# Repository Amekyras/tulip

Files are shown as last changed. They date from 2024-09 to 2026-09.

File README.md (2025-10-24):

# Welcome to TULIP 2.0

>"Everything will be alright as long as you have your -ing potato." - Mr. Tulip, to Mr. Pin, _The Truth_, by Terry Pratchett

>"See a pin and pick it up, and all day long you’ll have a pin!" - Stanley Howler, _Going Postal_, by Terry Pratchett

## A full pin mod for the AB motor mounts, XY gantry joints and front idler tensioners for the Voron v0.2
 - AB motors are mounted solidly to the frame, meaning no more shunting them back and forth with a bulky tensioning nut
 - AB motor shafts are held in double shear with an extra bearing, lowering radial force on the motor bearings
 - Tension is now applied through an M3 screw in the front idlers, and ALL bearing stacks run on pins rather than screws
 - Both MGN7H (stock) and MGN9C X rails are supported, WITH NO TRAVEL LOSS
 - Standard 3mm off-the-shelf pins, for those unable to cut their own
 - LazyCam support
 - Fysetc X light gantry compatibility (use standard XY joints)
 - Mamabot.io X light gantry support
 - Nema 17 AB Motor Mount Beta 
 - Nema 14 - 35mm Shaft Motor Mount Beta
 - Live Idler XY joints + Tension Idlers

## Installation
Go to the [Releases Page](https://github.com/Amekyras/tulip/releases) and download the .zip file from the latest release.

## Renders

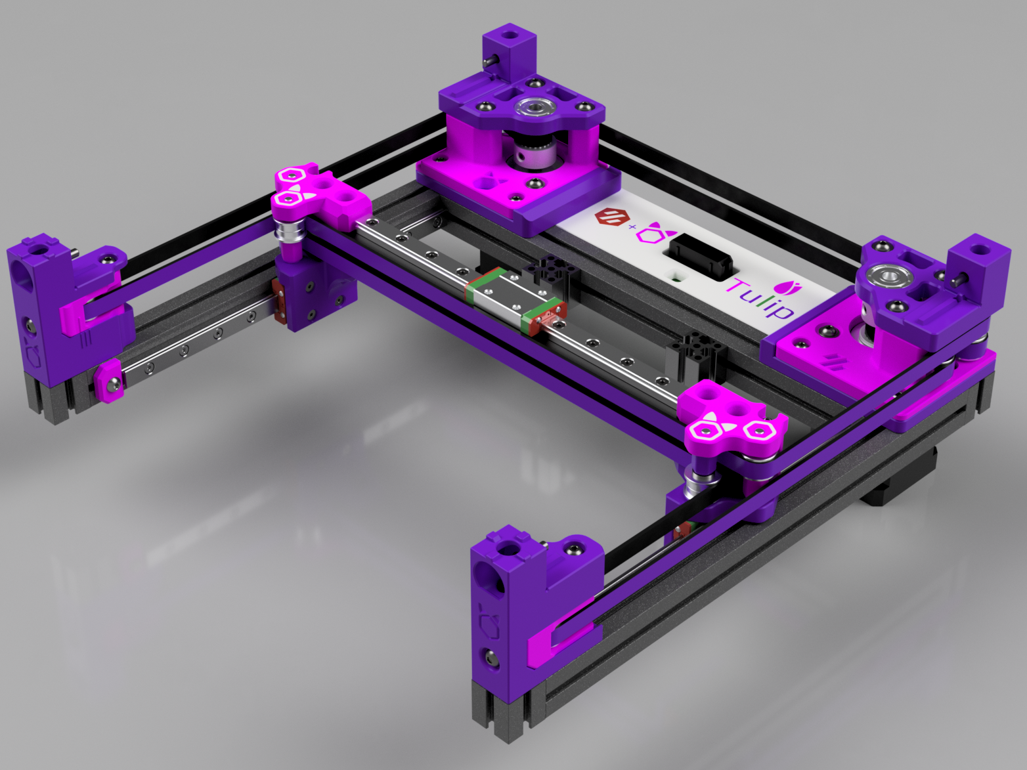
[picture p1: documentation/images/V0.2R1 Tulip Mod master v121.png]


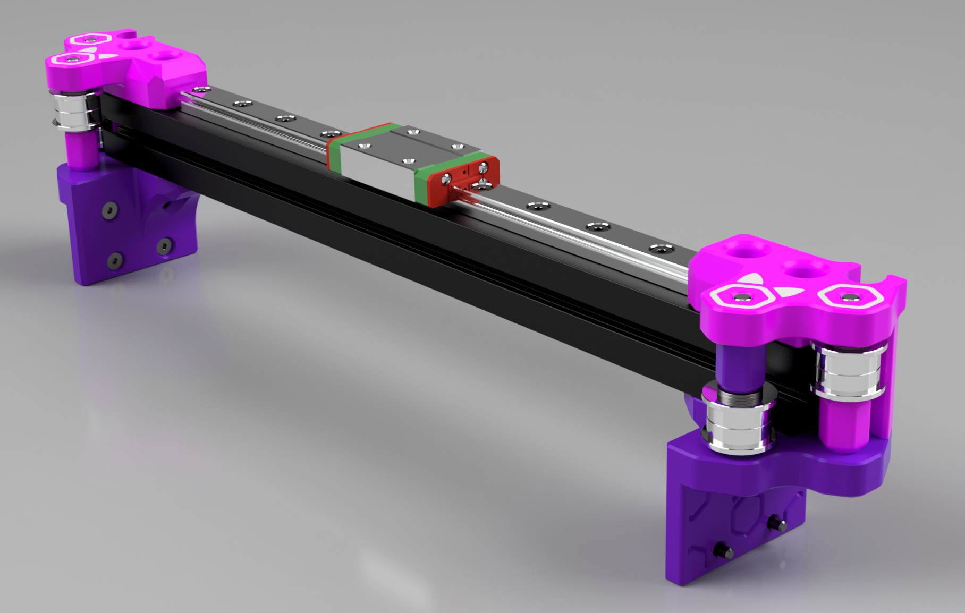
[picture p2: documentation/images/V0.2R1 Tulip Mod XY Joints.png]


| Idlers | XY Joints |
| :---: | :---: |
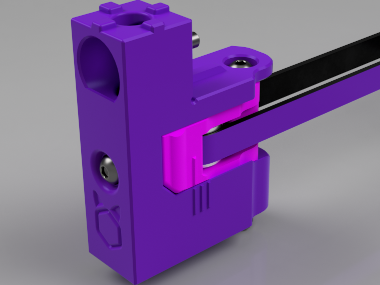
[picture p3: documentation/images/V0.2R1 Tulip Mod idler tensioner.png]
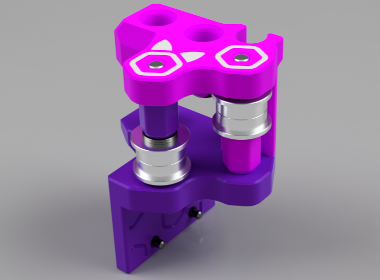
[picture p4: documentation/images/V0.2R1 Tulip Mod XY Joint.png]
|  |  |
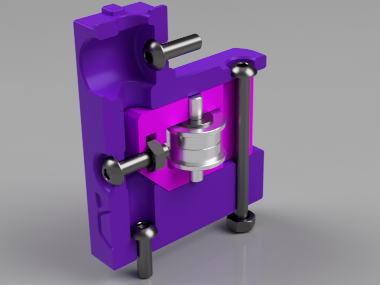
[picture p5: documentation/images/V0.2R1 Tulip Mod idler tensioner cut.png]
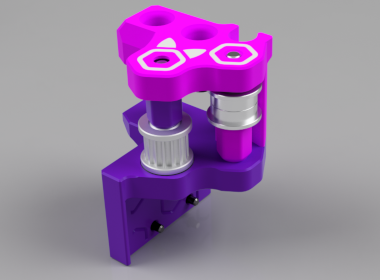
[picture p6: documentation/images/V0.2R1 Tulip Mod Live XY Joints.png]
|  |  |

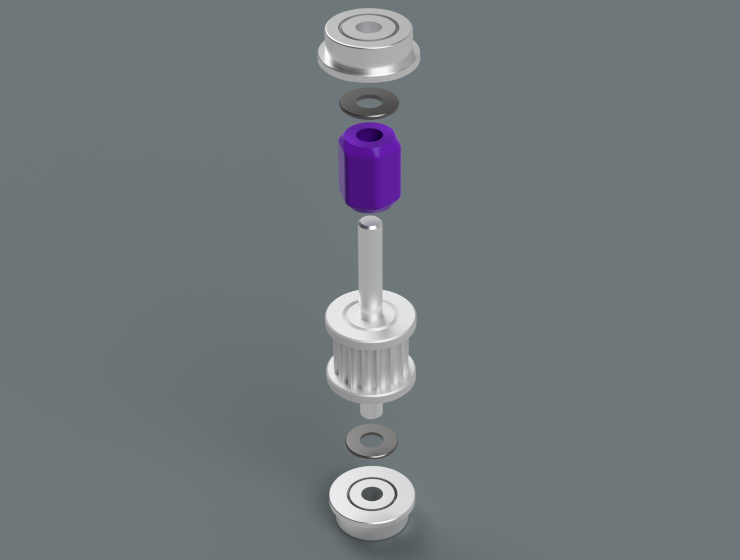
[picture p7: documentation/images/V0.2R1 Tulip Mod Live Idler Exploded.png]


----

> **Note - for LazyCam idlers you will require some extra printed parts to complete found [here](https://www.printables.com/model/533483-voron-02-lazycams-tool-free-locking-idlers-models)**

Parts required are; 

- LazyCams_C-A CamArm_v1.stl
- LazyCams_C-A CamLock_v1.stl

- LazyCams_C-B CamArm_v1.stl
- LazyCams_C-B CamLock_v1.stl

---

## Bill of Materials (BOM)

### Idler / Tensioner BOM

| **Part** | **Quantity** | **Notes / Links** | 
| :--- | :--- | :--- |
| Pin M3x18mm | 2 | [KB-3D](https://kb-3d.com/store/hardware/143-3mm-bearing-steel-shafts-various-lengths-1642291225169.html) / [AliExpress](https://www.aliexpress.us/item/3256804639701799.html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) | 
| M2x10 Self Tapper | 4 |  | 
| M3 Hexnut | 4 |  | 
| M3x0.5mm Washer / Shim | 4 |  | 
| M3x10 BHCS | 4 |  | 
| M3x12 BHCS | 2 |  | 
| M3x35 BHCS | 2 |  | 
| F623 Bearing | 4 |  | 

---

### AB Motor Mount BOM

| **Part** | **Quantity** | **Notes / Links** | 
| :--- | :--- | :--- |
| 625-ZZ/2RS Bearing | 2 |  | 
| GT2 20T 6mm Pulley | 2 |  | 
| M3 Hexnut | 6 |  | 
| M3 Threaded Insert | 4 |  | 
| M3x0.5mm Washer / Shim | 20 |  | 
| M3x8 BHCS | 2 |  | 
| M3x10 BHCS | 4 |  | 
| M3x12 BHCS | 4 |  | 
| M3x30 BHCS | 6 |  | 
| Pins M3x30mm | 4 | [KB-3D](https://kb-3d.com/store/hardware/143-3mm-bearing-steel-shafts-various-lengths-1642291225169.html) / [AliExpress](https://www.aliexpress.us/item/3256804639701799.html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) | 
| F623 Bearing | 12 |  | 

---

### XY Joint BOM

| **Part** | **Quantity** | **Notes / Links** | 
| :--- | :--- | :--- |
| M3x6 BHCS | 2 |  | 
| M2x6 FHCS | 8 |  | 
| M3x8 BHCS | 4 |  | 
| Pins M3x30mm | 4 | [KB-3D](https://kb-3d.com/store/hardware/143-3mm-bearing-steel-shafts-various-lengths-1642291225169.html) / [AliExpress](https://www.aliexpress.us/item/3256804639701799.html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) | 
| M3x0.5mm Washer / Shim | 16 |  | 
| F623 Bearing | 8 |  | 

---

### Live Idler XY Joint BOM

| **Part** | **Quantity** | **Notes / Links** | 
| :--- | :--- | :--- |
| M3x6 BHCS | 2 |  | 
| M2x6 FHCS | 8 |  | 
| M3x8 BHCS | 4 |  | 
| XY Pins M3x30 | 4 | [KB-3D](https://kb-3d.com/store/hardware/143-3mm-bearing-steel-shafts-various-lengths-1642291225169.html), [AliExpress](https://www.aliexpress.us/item/3256804639701799.html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) | 
| M3x0.5 Washer / Shim | 12 |  | 
| F623 Bearing | 8 |  | 
| 16T Solid Idler | 2 | [Alchemy3d](https://alchemy3d.de/products/active-idlers-5mm-id-16t-for-6mm-belt), [Filastruder](https://www.filastruder.com/collections/gates/products/gates-2gt-pulley-custom-no-grub-set-screw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), [3dkatten](http://3dkatten.eu/products/custom-16t-2gt-3mm-id-live-shaft-idler) | 

----

NEW Pin Hole Sizing for Tulip should mean NO MORE REAMING! but if you still have trouble fitting your pins then refer to this guide

> **Note - For PIN FITTING GUIDE you can find it [here](https://github.com/Amekyras/tulip/tree/main/PIN%20GUIDE)**

----

**Links to original source material**

https://github.com/VoronDesign/Voron-0

https://vorondesign.com

https://github.com/akinferno/Voron0/tree/main/LazyCams

https://github.com/ruiqimao/VoronUsers/tree/v0.2-mgn9c/printer_mods/ruiqimao/V0.2_MGN9C_X

**GNU Terry Pratchett**

----

**special thanx for all thoes who have helped with feedback and improvement ideas to get Tulip as good as it is!**

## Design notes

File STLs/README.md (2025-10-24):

# PRINTING GUIDE

All parts print with standard VORON Settings!

----

## CHOOSE YOUR JOURNEY

----

### OEM Tulip - The Path of Least Resistance

- One set of
  - AB Mounts
  - XY Joints
  - Idler Tensioners
  - Umbilical Covers
  - Tools & Jigs

----  

### LIVE Tulip - The Intrepid Adventurer

- One set of
  - AB Mounts
  - Live XY Joints
  - Live Idler Tensioners
  - Umbilical covers
  - Tools & Jigs

----

### EXPERIMENTAL Tulip - The Undaunted Explorer

- A Choice of optional parts are available to you to experiment with
- WARNING !!! This section is for those who have good knowledge of their printer, understand the CAD and work / assembly of these parts

  - S35 AB Mounts - For 35mm Shaft Nema14 Motors
  - Nema17 AB Mounts
  - Nema17 AWD AB Mounts
  - Mamababot.IO XY joints

----

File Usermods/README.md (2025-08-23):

| Creator | Mod title | Description |
| --- | --- | --- |
| hawk16zz | [2mm taller parts](<./hawk16zz/2mm%20Taller%20ABs%20and%20Blocks>)| 2mm taller mod to address heights descripencies due to door mods and/or panels|

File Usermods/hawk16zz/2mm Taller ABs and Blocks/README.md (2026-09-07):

2026-09-06: Updated for Tulip v2.1

This mod adds 2mm to the height of A/B tops and the tensioner block parts to address issues with the LDO fridge door kit sitting proud on some builds or if you need them for full height panels.

The increase in height also means you don't need the lazycam specific tensioner carriage as they are no long are in the path of the cam lever arm.

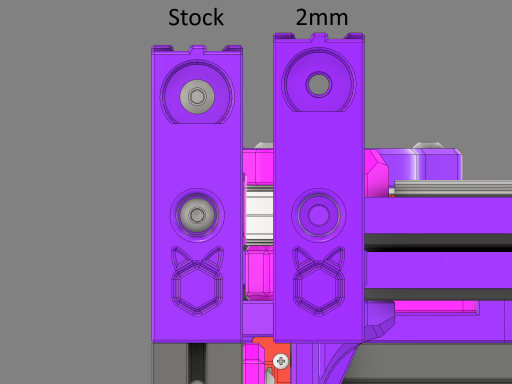
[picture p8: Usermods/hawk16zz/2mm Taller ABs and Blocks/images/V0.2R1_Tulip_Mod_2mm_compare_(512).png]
A comparison of stock v 2mm taller.


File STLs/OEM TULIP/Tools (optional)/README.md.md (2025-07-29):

The TOOLS provided for Tulip Mod carry a certain element of risk to the user!

if not used correctly these can injure / maim you so please use them wisely!

They are intended to help you cut and / or install parts for Tulip Mod.

If you have any doubt or questions about the safe use of these tools please reach out on the Voron Discord to either @driftrotor or @amekyras and we will do our best to guide you and answer any questions you might have.
We accept no resposibility for any injury / damage to property or persons involved and all use of these tools is solely the resposibility of the person using them.

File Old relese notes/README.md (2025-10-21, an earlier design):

----

### 01/12/24

CAD V33 release

updated the pin cutting tool to give 18mm pins (as this is now the standard)

STL's have been updated

28/11/24

CAD v32 release

small amendments to supporting drawing

removal of 16mm pin tension idlers - in favour of better 18mm pin version (also to simplify and cause less confusion)

NEW addition of Nema 14 - 35mm shaft CAD and STL's

NEW addition of LIVE IDLER CAD for XY joints to have solid toothed idler and live pins
STL's have been added

----

### 10/11/24

CAD v31 release

Added umbilical Cover Plates (with + without Bowden Hole) and MMU versions

Added Picobilical Strain Relief Beta (MMU)

----

### 04/11/24

CAD v29 release

House keeping in CAD - Created componants for all bodies, Some name corrections, Reduced Materials

18mm Pin version of the front Idler Tensioners have been added for those who are struggling to find 16mm Pins, These also have LazyCam support
these are also recomended to those wishing to use GT3 belts

X Light Gantry (MamaBot.io) Beta is now included
> **Note - This is NOT compatible with the Fysetc X Light Gantry, instead use standard XY Joints**

Nema 17 AB Motor Mount Beta added for testing

ReadMe's added for some folders - please make sure you read them

STL's added

BOM amended + PDF format added

ALL STL's updated to latest CAD version

ALL Pin Holes have a new size (this should work for a better fit withoit the reeming)

----

### 16/09/24

CAD v28 release

Both Standard and LazyCAM static bodies have has the access hole size changed (for the front fixing into the extrusion) so that longer screws can be used and dropped in from the top.

A NEW motor "Pully Tool" has been made to measure from the motor tops rather than from the top of the shaft

BOM has been updated to show "Washers / Shims" for the bearing stacks

XY_Upper_Joint Fixings changed from M3x6mm to M3x8mm on CAD

PIN GUIDE has been added to help users get the best from TULIP

MGN9H BETA (yes H) has been added for those wanting to use this type of rail setup. All printed parts needed are in the STL's frolder MGN9H.
> **Note - A 160mm Rail is required for full travel**

----

### 04/09/24

CAD v27 release

Amended Pin hole depth on parts

- Top_Mount_A_MGN9C_x1
- Top_Mount_B_MGN9C_x1

Motor "Pully Tool" has now been added to help get them in the right place

Picture of the tool has been added to the PICS folder

STL's have been updated for the latest change for the parts affected

----

### 24/08/24

CAD v26 release

CAD names have been updated to be consistant with the STL names and the [a] for accent colour marking has also been added. Corrected a mistake where the Voron Logo was mirrored on Mid_Mount_A_x1.

STL's Updated to latest Names denoting the [a] for accent colours. corrected Mid_Mount_A_x1 STL

----

### 08/08/24

CAD v25 release

Idler tensioners static body had printability update to make B side easier to print (less chance to warp off the bed)

tensioner upers had changes to work with new static bodies

Tensioner lowers captive nut minor geometry changes - better pre-engagement with tension screw - reduced hole size after captive nut to act as tension screw "nylock"

LazyCam static bodies added for those wishing to use the LazyCam system (type C)

----

### 10/07/24

CAD v24 release

Idler tensioners static body is now one piece and printed on its side

Idler tensioners lock screw is now static with slot in tensioner parts

XY joints had some holes resized and some minor corrections

Spacers - new fillet chamfer design (fillamfer)

AB Motor mounts plates and mid parts have locating tabs to secure each other together for more secure umbilical plate attachment

Tools added - Bearing insert tool & Drill jig for access to tensioner locking screw

----

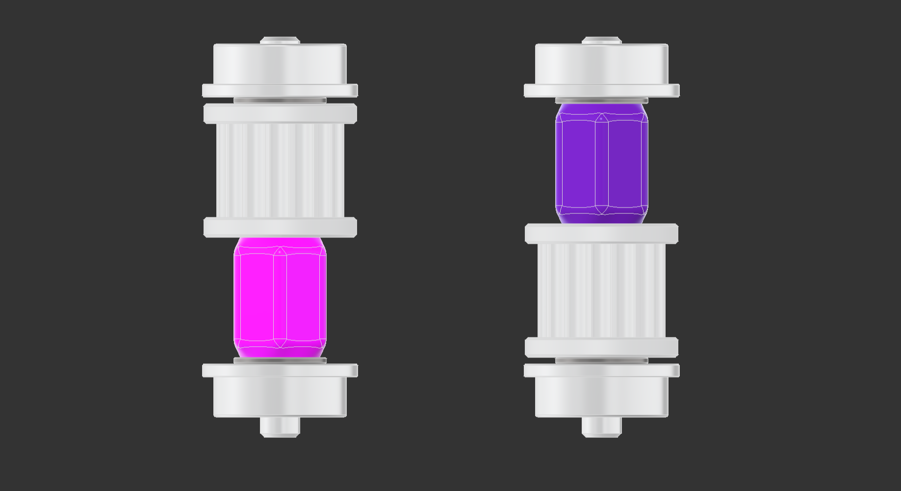
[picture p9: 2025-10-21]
Pics/Live Idler Stack.png

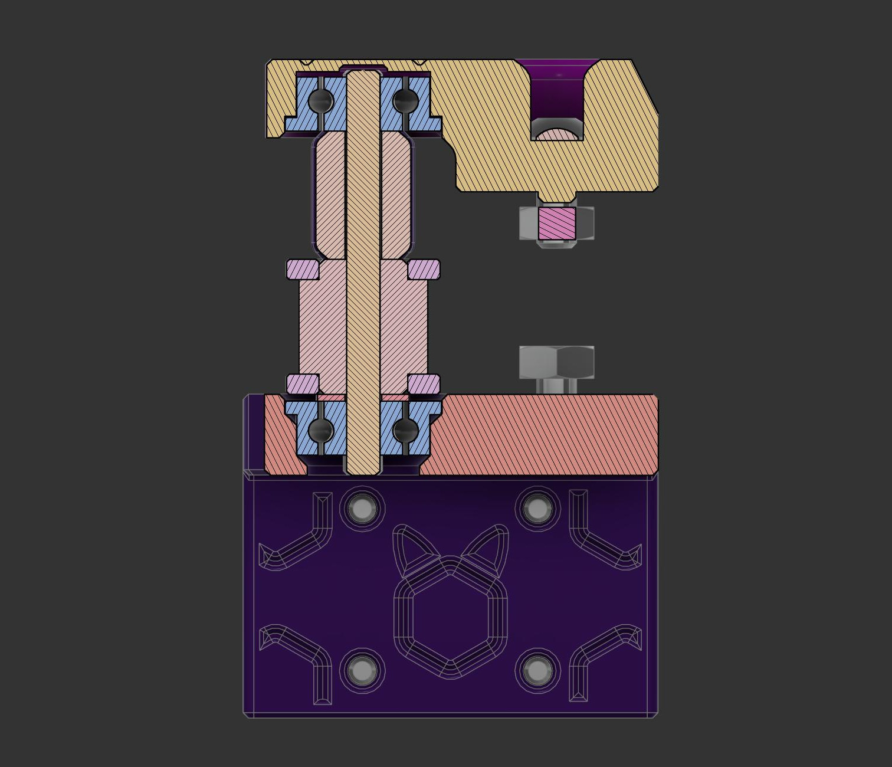
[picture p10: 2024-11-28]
documentation/images/V0.2R1 XY Live Idler Cut.jpg

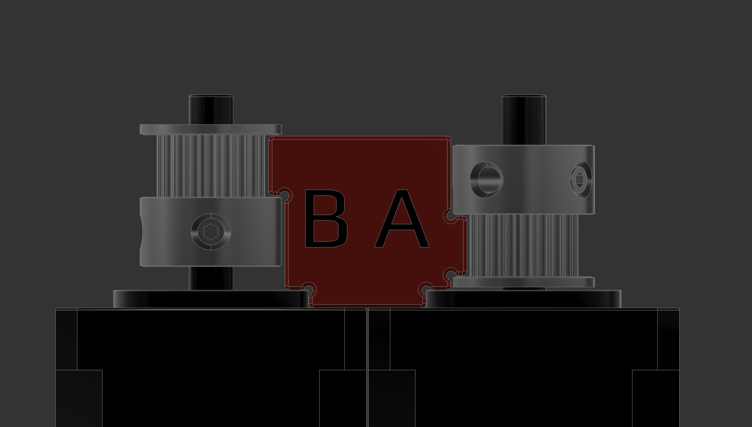
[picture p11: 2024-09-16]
documentation/images/Pulley Tool.png

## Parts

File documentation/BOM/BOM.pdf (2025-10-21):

### BOM

Part | Qty | link

Idler / Tensioner BOM

Pin M3x18mm | 2
M2x10 Self Tapper | 4
M3 Hexnut | 4
M3x0.5mm Washer / Shim | 4
M3x10 BHCS | 4
M3x12 BHCS | 2
M3x35 BHCS | 2
F623 bearing | 4

AB Motor Mount BOM

625 - ZZ / 2RS Bearing | 2
GT2 20T 6mm Pulley | 2
M3 Hexnut | 6
M3 Threaded Insert | 4
M3x0.5mm Washer / Shim | 20
M3x8 BHCS | 2
M3x10 BHCS | 4
M3x12 BHCS | 4
M3x30 BHCS | 6
Pins M3x30mm | 4
F623 bearing | 12

XY Joint BOM

M3x6 BHCS | 2
M2x6 FHCS | 8
M3x8 BHCS | 4
Pins M3x30mm | 4
M3x0.5mm Washer / Shim | 16
F623 bearing | 8

Live Idler XY Joint BOM

M3x6 BHCS | 2
M2x6 FHCS | 8
M3x8 BHCS | 4
XY Pins M3x30 | 4
M3x0.5 Washer / Shim | 12
F623 bearing | 8
16 tooth solid idler | 2
KB-3D (https://kb-3d.com/store/hardware/143-3mm-bearing-steel-shafts-various-lengths-1642291225169.html) | Ali-Express (https://www.aliexpress.us/item/3256804639701799.html)
KB-3D (https://kb-3d.com/store/hardware/143-3mm-bearing-steel-shafts-various-lengths-1642291225169.html) | Ali-Express (https://www.aliexpress.us/item/3256804639701799.html)
KB-3D (https://kb-3d.com/store/hardware/143-3mm-bearing-steel-shafts-various-lengths-1642291225169.html) | Ali-Express (https://www.aliexpress.us/item/3256804639701799.html)
KB-3D (https://kb-3d.com/store/hardware/143-3mm-bearing-steel-shafts-various-lengths-1642291225169.html) | Ali-Express (https://www.aliexpress.us/item/3256804639701799.html)
filastruder.com (https://www.filastruder.com/collections/gates/products/gates-2gt-pulley-custom-no-grub-set-screw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) | Alchemy3d (https://alchemy3d.de/products/active-idlers-5mm-id-16t-for-6mm-belt) | 3dkatten (http://3dkatten.eu/products/custom-16t-2gt-3mm-id-live-shaft-idler)

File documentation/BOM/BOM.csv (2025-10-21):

Part | Qty | link
Idler / Tensioner BOM
Pin M3x18mm | 2 | KB-3D Ali-Express
M2x10 Self Tapper | 4
M3 Hexnut | 4
M3x0.5mm Washer / Shim | 4
M3x10 BHCS | 4
M3x12 BHCS | 2
M3x35 BHCS | 2
F623 bearing | 4
AB Motor Mount BOM
625 - ZZ / 2RS Bearing | 2
GT2 20T 6mm Pulley | 2
M3 Hexnut | 6
M3 Threaded Insert | 4
M3x0.5mm Washer / Shim | 20
M3x8 BHCS | 2
M3x10 BHCS | 4
M3x12 BHCS | 4
M3x30 BHCS | 6
Pins M3x30mm | 4 | KB-3D Ali-Express
F623 bearing | 12
XY Joint BOM
M3x6 BHCS | 2
M2x6 FHCS | 8
M3x8 BHCS | 4
Pins M3x30mm | 4 | KB-3D Ali-Express
M3x0.5mm Washer / Shim | 16
F623 bearing | 8
Live Idler XY Joint BOM
M3x6 BHCS | 2
M2x6 FHCS | 8
M3x8 BHCS | 4
XY Pins M3x30 | 4 | KB-3D Ali-Express
M3x0.5 Washer / Shim | 12
F623 bearing | 8
16 tooth solid idler | 2 | filastruder.com Alchemy3d 3dkatten

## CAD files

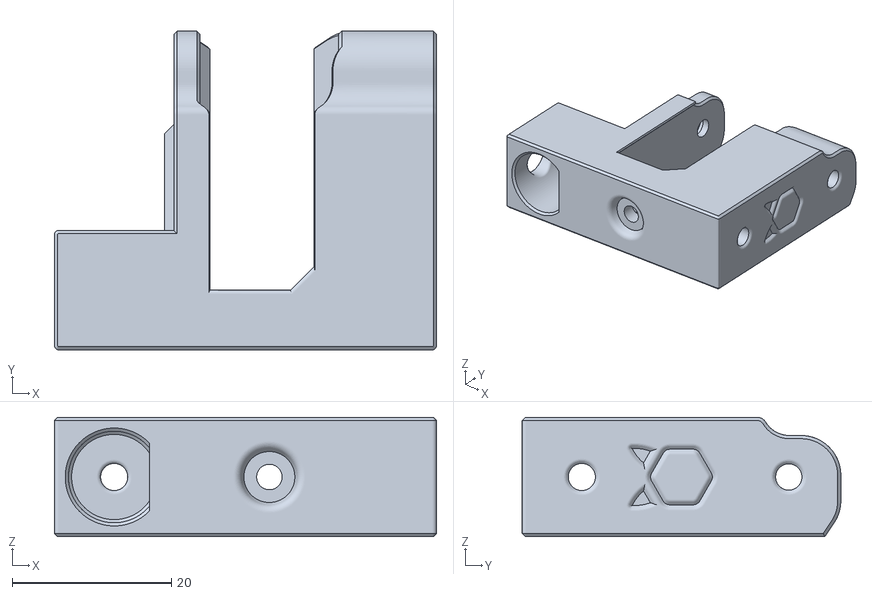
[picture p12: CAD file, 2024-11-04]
STLs/B_Idler_Static_x1.stl
48.0 x 40.0 x 15.0

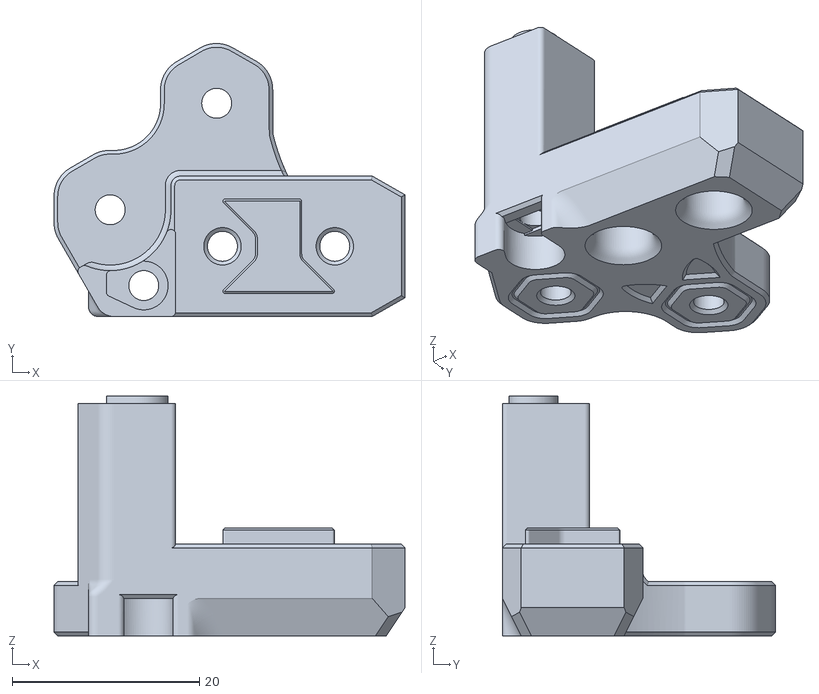
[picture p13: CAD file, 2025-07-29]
STLs/EXPERIMENTAL TULIP/Mamabot.io X Light Gantry Beta/[a]_XY_Joint_Left_Upper.stl
37.5 x 29.2 x 25.6

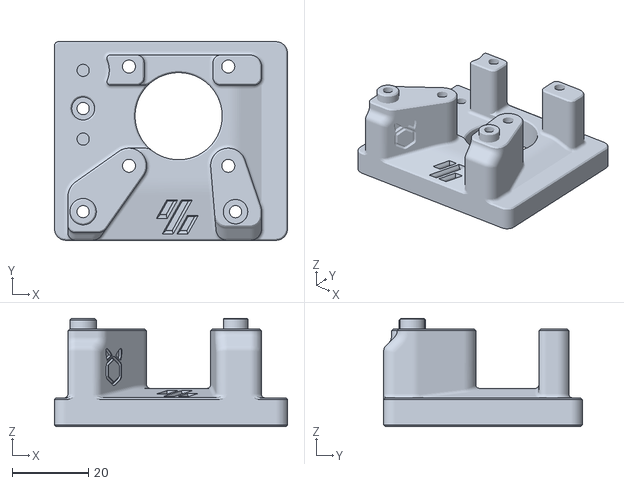
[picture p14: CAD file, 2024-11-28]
STLs/EXPERIMENTAL TULIP/NEMA14-S35 MGN9H/[a]_Mid_Mount_B_MGN9H_x1.stl
61.0 x 52.0 x 28.3

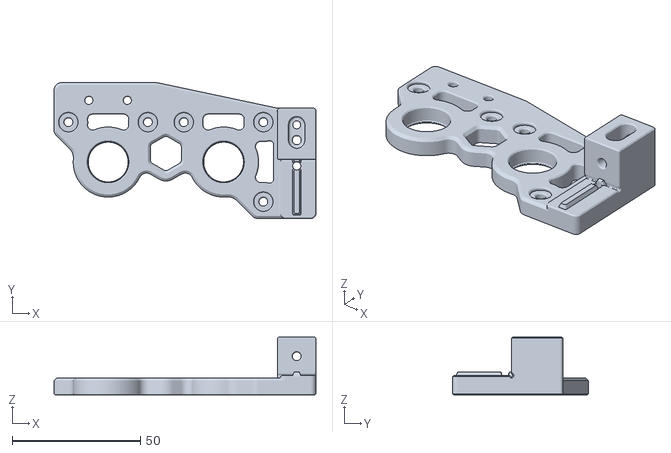
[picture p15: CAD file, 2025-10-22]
STLs/EXPERIMENTAL TULIP/Nema17 2.0 AWD/Top_Mount_AB_x1.stl
102.1 x 53.0 x 22.5

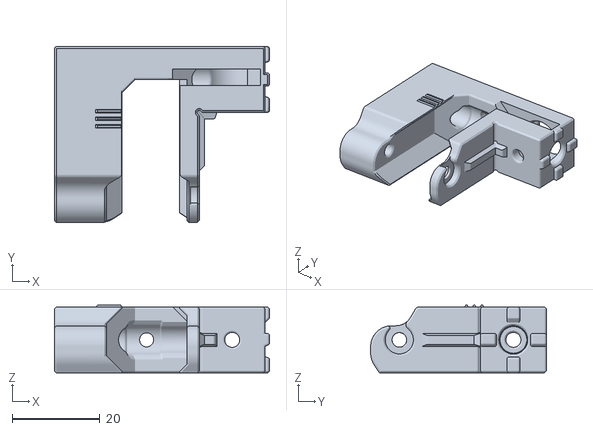
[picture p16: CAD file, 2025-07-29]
STLs/LIVE TULIP/Live Idler tensioners/Live Lazy Cam Tension Idlers (optional)/B_Live_Idler_Static_LazyCam_x1.stl
49.0 x 40.0 x 15.4

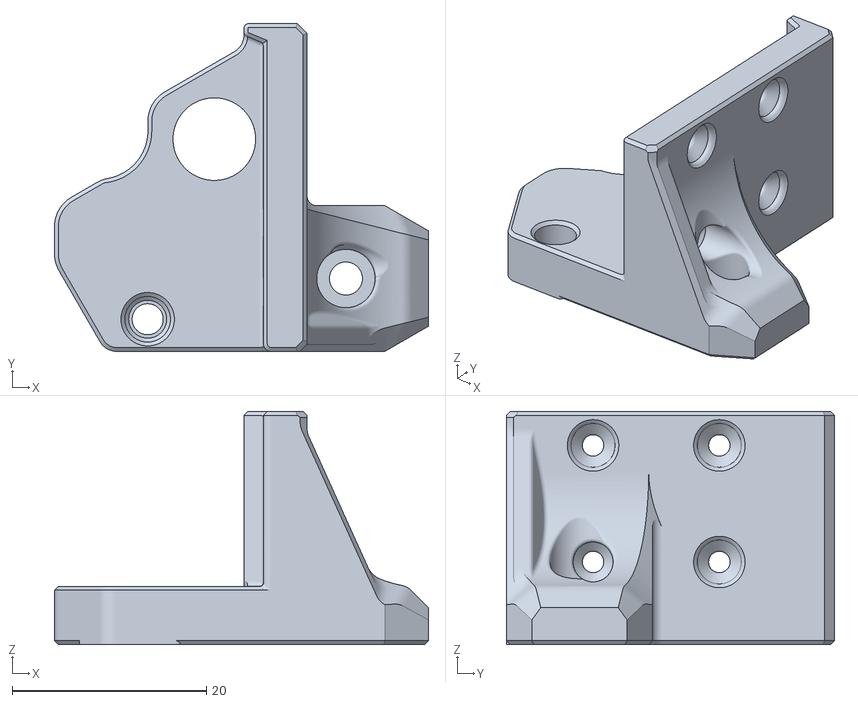
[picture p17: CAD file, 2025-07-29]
STLs/LIVE TULIP/Live XY joints/Live XY Joints/Live_XY_Joint_Left_Lower.stl
38.5 x 33.7 x 24.0

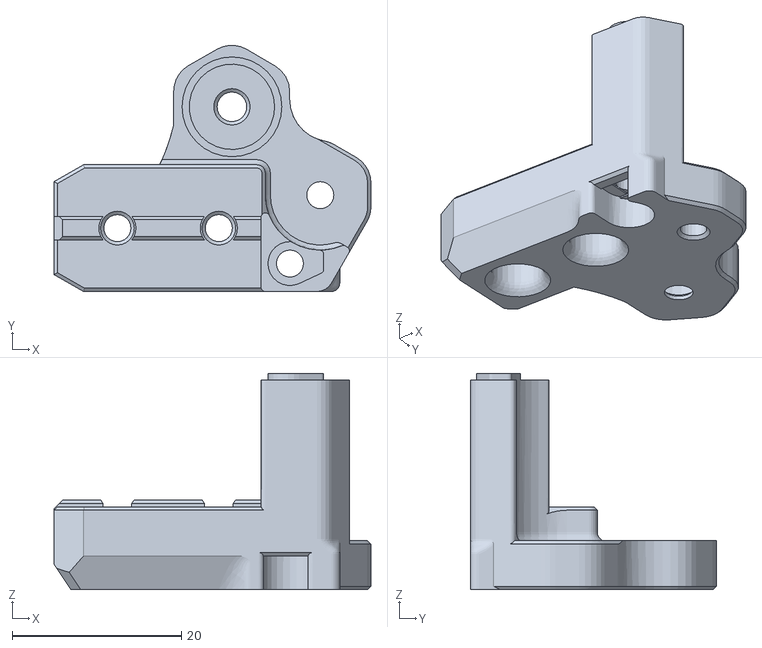
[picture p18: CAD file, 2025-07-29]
STLs/LIVE TULIP/Live XY joints/MMU XY Upper Part (optional)/Live_XY_Right_Upper_MMU.stl
37.5 x 29.1 x 25.6

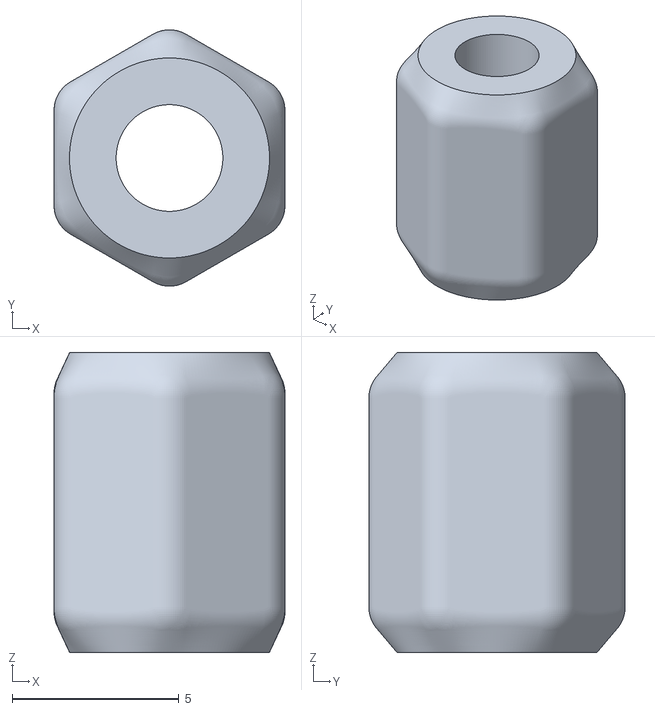
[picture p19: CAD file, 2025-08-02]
STLs/LIVE TULIP/Spacer_Hex_x6.stl
6.93 x 7.69 x 9.00

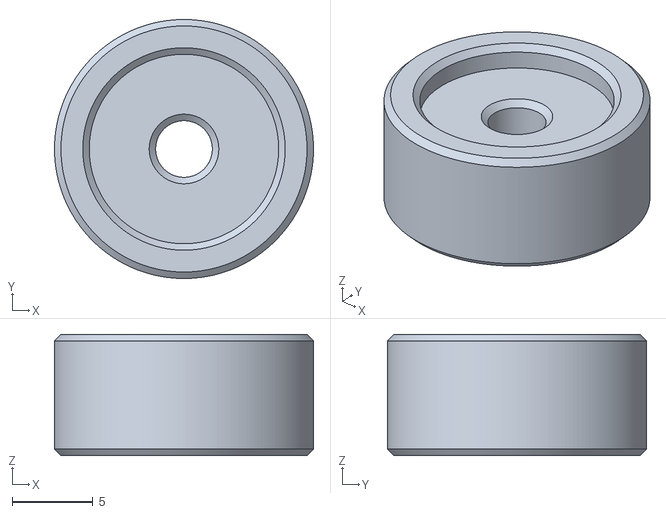
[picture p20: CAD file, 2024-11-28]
STLs/LIVE TULIP/Tools (optional as needed)/Right_Idler_Tool.stl
16.0 x 16.0 x 7.50

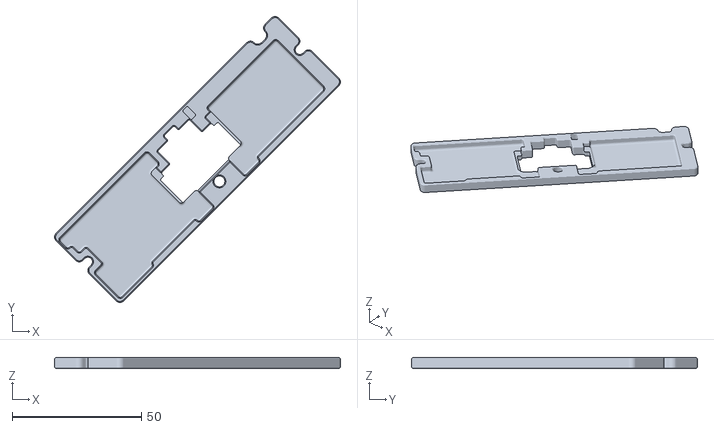
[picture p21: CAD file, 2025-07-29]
STLs/LIVE TULIP/Umbilicals (optional)/PicoBilical/Cover_Plate.stl
110.8 x 110.8 x 4.20

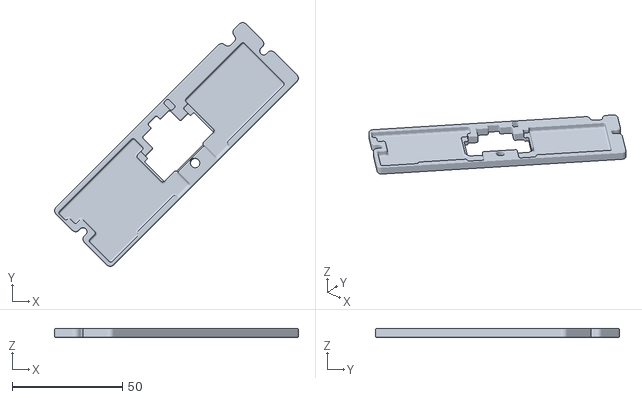
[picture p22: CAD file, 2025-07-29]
STLs/LIVE TULIP/Umbilicals (optional)/PicoBilical/MMU (optional)/Cover_Plate_MMU.stl
110.8 x 110.8 x 4.20

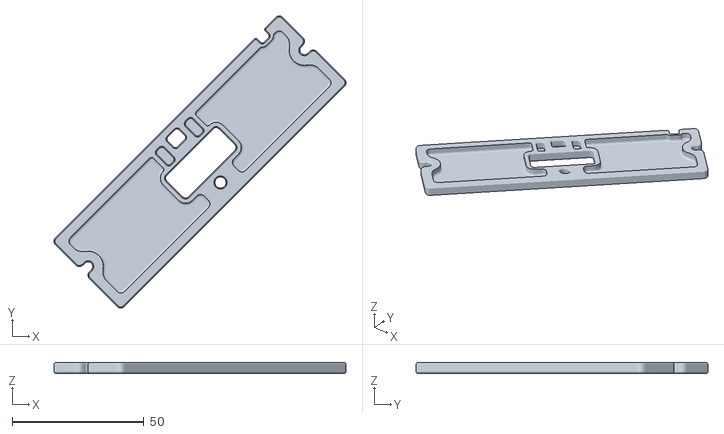
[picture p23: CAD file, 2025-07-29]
STLs/LIVE TULIP/Umbilicals (optional)/Standard Umbilical/MMU (optional)/Umbilical_Plate_MMU.stl
110.8 x 110.8 x 4.00

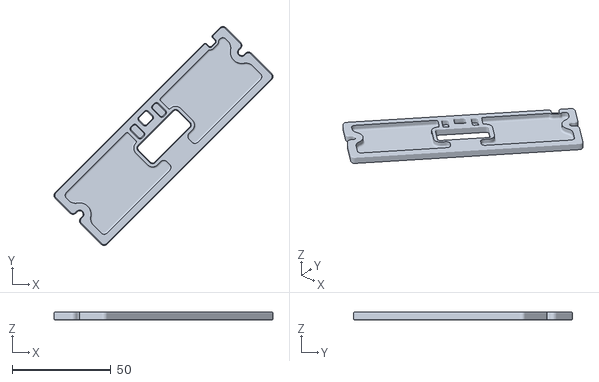
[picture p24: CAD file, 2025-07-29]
STLs/LIVE TULIP/Umbilicals (optional)/Standard Umbilical/Umbilical_Plate_No_Bowden_Hole_x1.stl
110.8 x 110.8 x 4.00

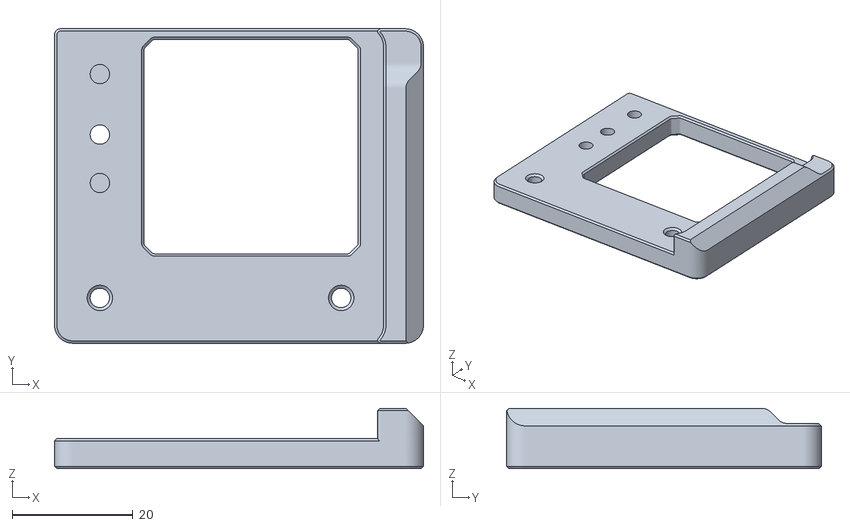
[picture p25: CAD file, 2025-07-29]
STLs/OEM TULIP/AB Mounts/Mount_Plate_B_x1.stl
61.0 x 52.0 x 10.00

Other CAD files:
STLs/EXPERIMENTAL TULIP/NEMA14-S35/[a]_Mid_Mount_B_MGN9C_x1.stl
STLs/LIVE TULIP/Live Idler tensioners/Live Tension Idlers/B_Live_Idler_Static_x1.stl
STLs/OEM TULIP/Idler-Tensioners/[a]_Idler_A_Tensioner_Upper_x1.stl
STLs/OEM TULIP/Idler-Tensioners/LazyCams (optional)/A_Idler_Static_LazyCam_x1.stl
STLs/EXPERIMENTAL TULIP/Mamabot.io X Light Gantry Beta/[a]_XY_Joint_Right_Upper.stl
STLs/EXPERIMENTAL TULIP/NEMA14-S35 MGN9H/Top_Mount_A_MGN9H_x1.stl
STLs/EXPERIMENTAL TULIP/NEMA14-S35 MGN9H/Top_Mount_B_MGN9H_x1.stl
STLs/EXPERIMENTAL TULIP/NEMA14-S35 MGN9H/[a]_Mid_Mount_A_MGN9H_x1.stl
STLs/EXPERIMENTAL TULIP/NEMA14-S35/Top_Mount_A_MGN9C_x1.stl
STLs/EXPERIMENTAL TULIP/NEMA14-S35/Top_Mount_B_MGN9C_x1.stl
STLs/EXPERIMENTAL TULIP/NEMA14-S35/[a]_Mid_Mount_A_MGN9C_x1.stl
STLs/EXPERIMENTAL TULIP/NEMA14-S35/[a]_XY_Joint_spacer_hex_x2.stl
STLs/EXPERIMENTAL TULIP/Nema 17 2.0/Mount_Plate_A_x1.stl
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

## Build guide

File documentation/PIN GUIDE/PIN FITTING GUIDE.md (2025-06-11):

# PIN-FITTING-GUIDE

This is to help get your PINS fitted in your newly printed TULIP mod.

TOOLS YOU WILL NEED

 - Digital Vernier Calipers (to two decimal places).
 - 3mm Drill Bit.
 - Drill.
 - 3mm PINS

You may have noticed that the PIN holes for TULIP are slightly too small / tight.
This is not unintended and has been carefully designed this way.
To PRINT the PERFECT hole size for the PINS is almost impossible as there are far too many veriables. (extrusion, XY compensation, Material etc)
So this method has been devised in order for ALL users of TULIP to get the same results.

The pictures below shows the differnece between the PIN diameter and the TYPICAL SCREW diameter (M3 threaded).
This is the difference between getting a nice fit for your bearings to be properly restrained so they work more effectively.
The PIN hole diameter is also just as crucial and the difference between getting a nice PRESS FIT / INTERFERENCE FIT and a LOOSE FIT is about 0.1 – 0.15mm (diameter) or 0.05 – 0.075mm (radius).

SCREW Dia

PIN Dia

The PIN holes in the CAD are 3.1mm and with (ABS) meterial shrinkage as approx 0.6% so in theory we should end up with a 3.08mm hole.
But in reality you are more likely to end up with what i have below (2.94mm) as material is dragged into the centre of the circle while material is being extruded. This TYPICALLY can be (Dialed In) by using XY compensation on interanl holes in your slicer.

PIN HOLE Dia

But for many we dont tend to tune in these settings, so we need to **REAM** out the PIN holes in order to get that nice **SNUG** fit.

Get your 3mm DRILL BIT and measure with your CALLIPERS to make sure it is no more that 3mm. (lets face it, you just spend a few hours printing the parts, you dont want to ruin them now)

DRILL BIT Dia

REEMING

> **Note - After you have confirmed they are good CAREFULLY REAM out the PIN HOLES!**

Make sure to go **SLOW** here, it is easy to go too **FAST** and **RUIN** your prints! (ASK ME HOW I KNOW)

PIN HOLE Dia after REEMING

Fitted PIN

Now that we have **REAMED** the **PIN** holes you can now fit your **PINS**
It should be a Good Snug Press Fit - This will mean that your PINS will stay PUT for a long time!

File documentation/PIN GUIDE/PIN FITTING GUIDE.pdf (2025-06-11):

PIN-FITTING-GUIDE

This is to help get your PINS fitted in your newly printed TULIP mod.

TOOLS YOU WILL NEED

- Digital Vernier Calipers (to two decimal places).
- 3mm Drill Bit.
- Drill.
- 3mm PINS

You may have noticed that the PIN holes for TULIP are slightly too small / tight.
This is not unintended and has been carefully designed this way.
To PRINT the PERFECT hole size for the PINS is almost impossible as there are far too many variables. (extrusion, XY compensation, Material etc)
So this method has been devised in order for ALL users of TULIP to get the same results.

The pictures below shows the difference between the PIN diameter and the TYPICAL SCREW diameter (M3 threaded).

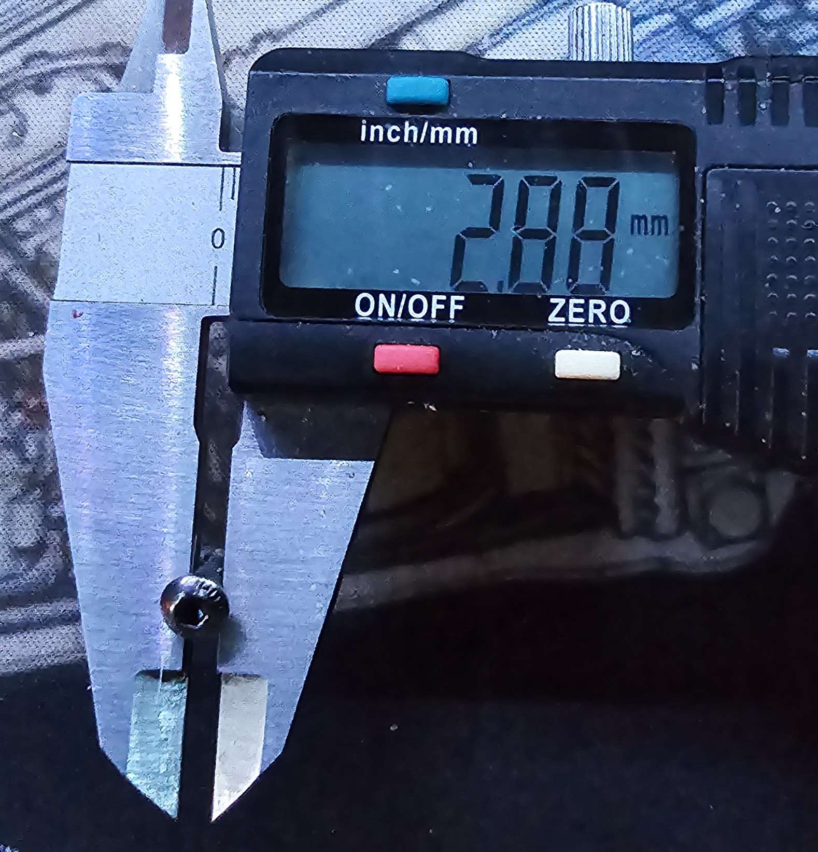
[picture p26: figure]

This is the difference between getting a nice fit for your bearings to be properly restrained so they work more effectively.

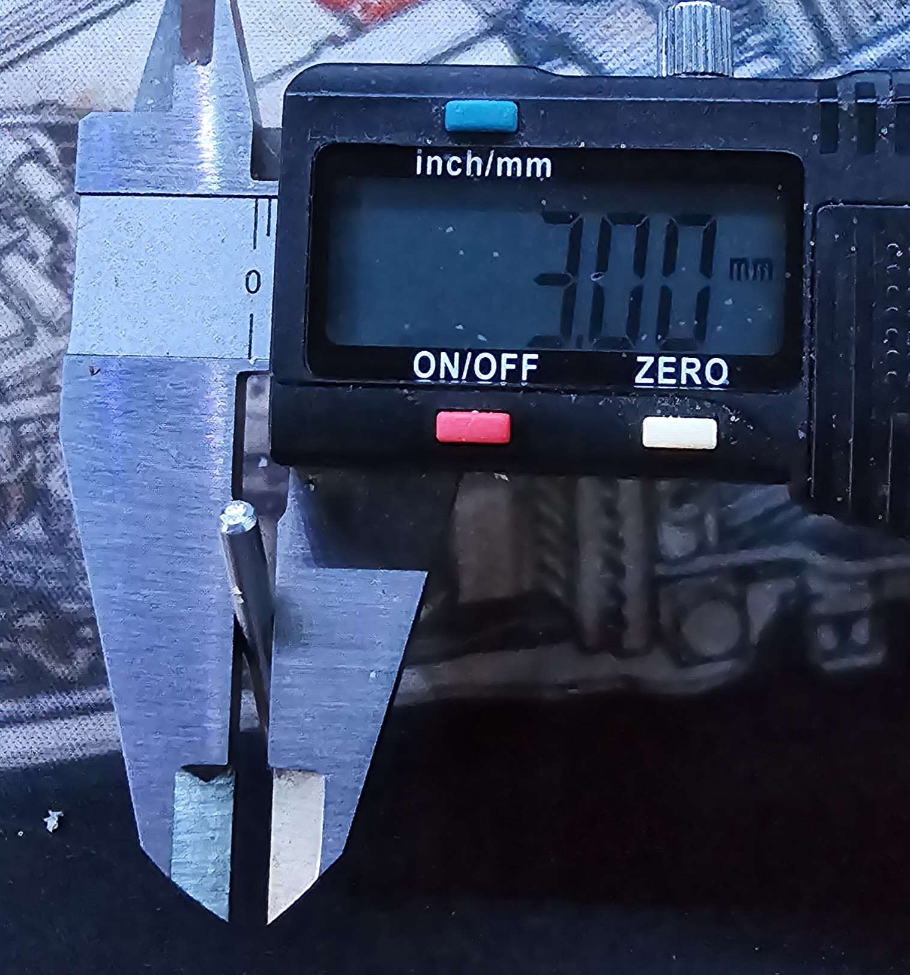
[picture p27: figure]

The PIN hole diameter is also just as crucial and the difference between getting a nice PRESS FIT / INTERFERENCE FIT and a LOOSE FIT is about 0.1 – 0.15mm (diameter) or 0.05 – 0.075mm (radius).
So if the PIN hole is slightly too big (3.12 as opposed to 3.0mm) it is the difference between having a RELIABLE mod or one that will FAIL to deliver.

The PIN holes in the CAD are 3.1mm and with (ABS) meterial shrinkage as approx 0.6% so in theory we should end up with a 3.08mm hole.
But in reality you are more likely to end up with what i have below (3.94mm) as material is dragged into the centre of the circle while material is being extruded. This TYPICALLY can be (Dialed In) by using XY compensation on interanl holes in your slicer.

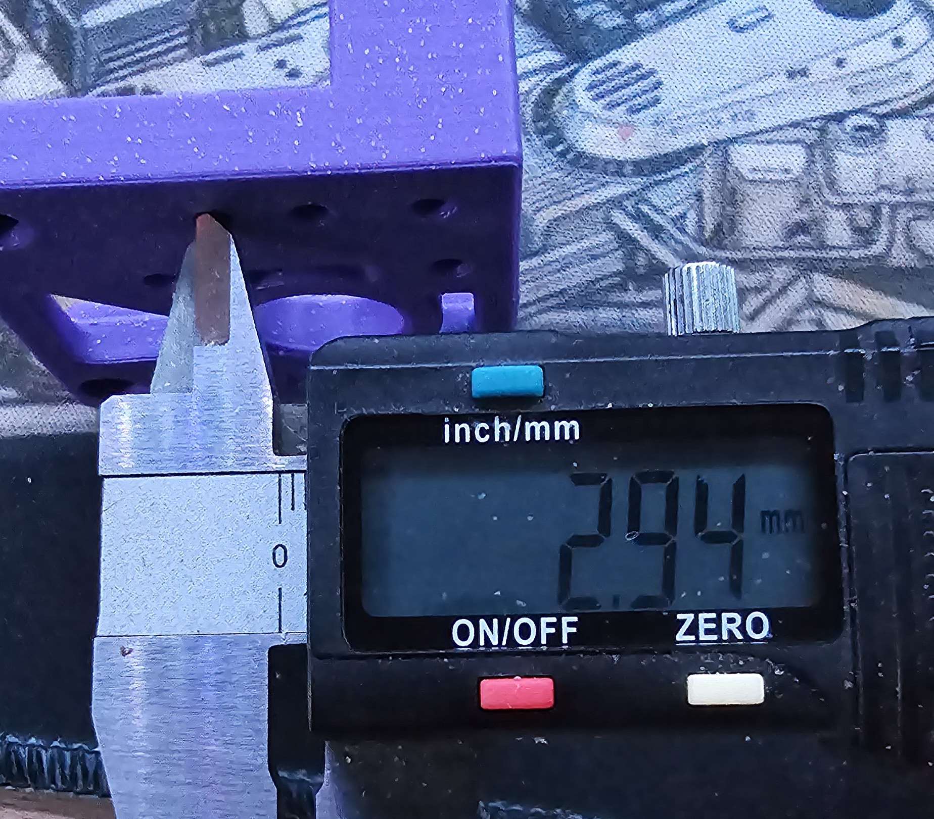
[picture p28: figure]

But for many we dont tend to tune in these settings, so we need to **REAM** out the PIN holes in order to get that nice **SNUG** fit.

Get your 3mm DRILL BIT and measure with your CALLIPERS to make sure it is no more that 3mm. (lets face it, you just spend a few hours printing the parts, you dont want to ruin them now)

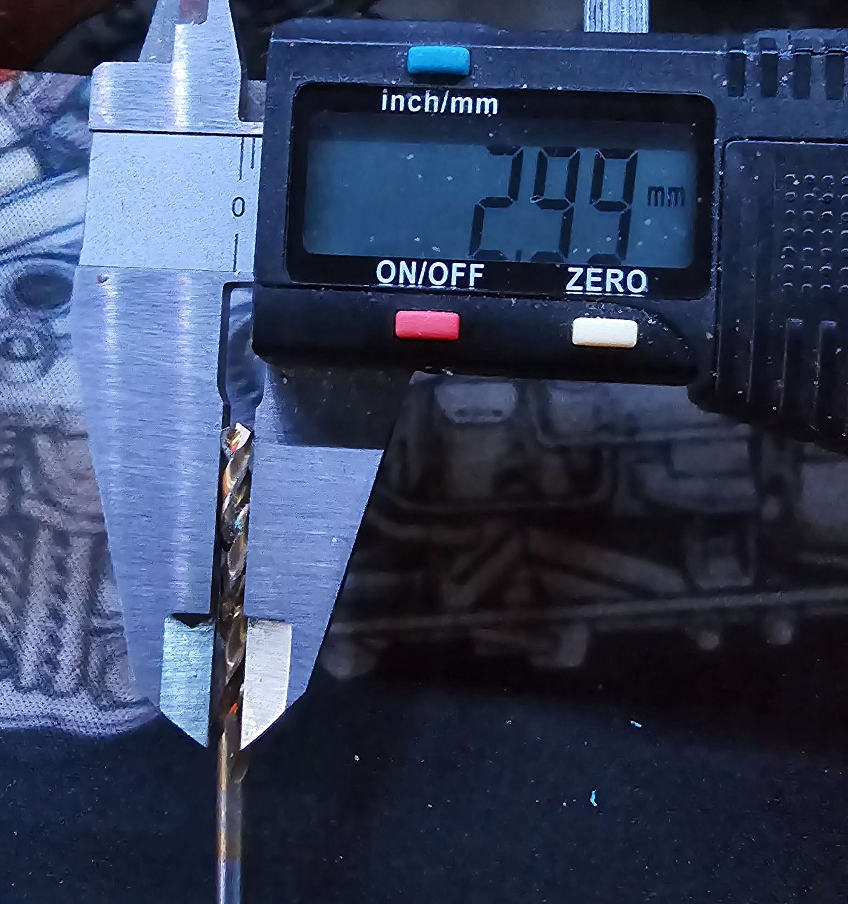
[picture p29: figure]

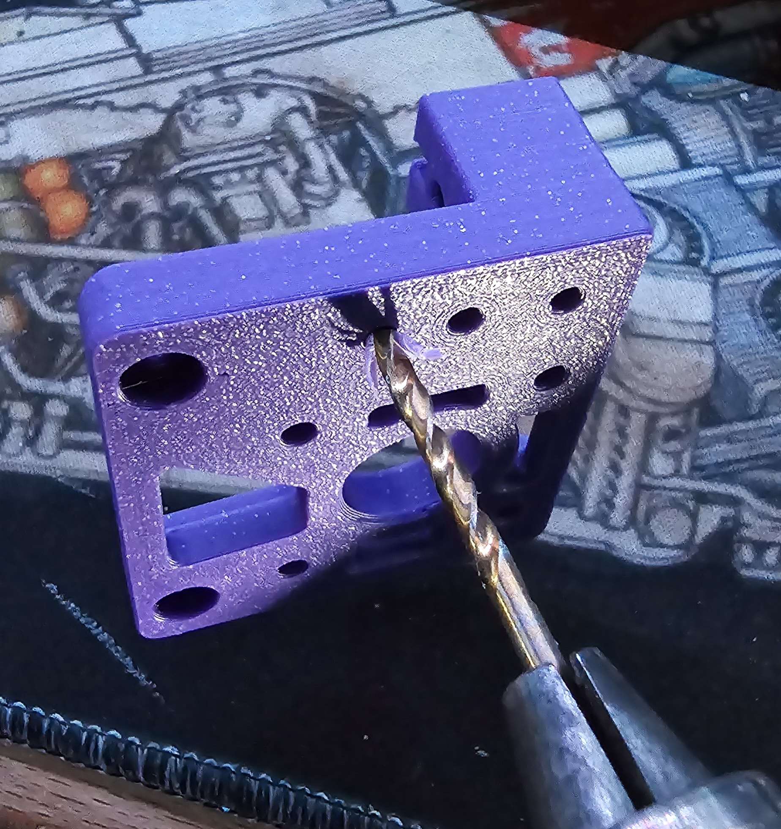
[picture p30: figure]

After you have confirmed they are good CAREFULLY REAM out the PIN HOLES!

Make sure to go **SLOW** here, it is easy to go too **FAST** and **RUIN** your prints! (ASK ME HOW I KNOW)

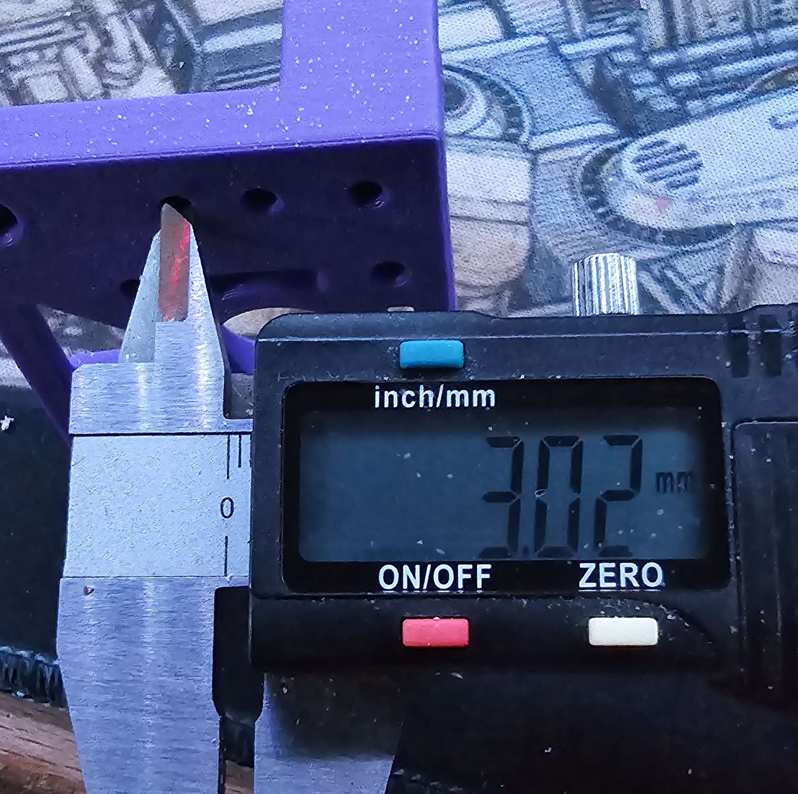
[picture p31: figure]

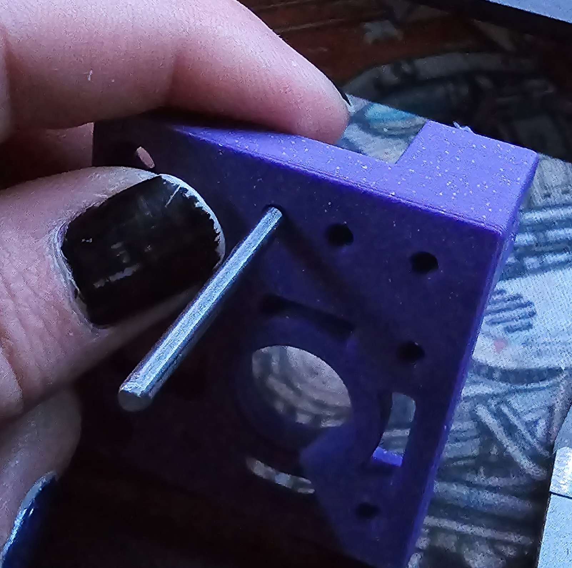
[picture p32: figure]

Now that we have **REAMED** the **PIN** holes you can now fit your **PINS**
It should be a Good Snug Press Fit - This will mean that your PINS will stay PUT for a long time!

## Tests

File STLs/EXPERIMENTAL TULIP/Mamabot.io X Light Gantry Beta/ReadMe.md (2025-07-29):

Please note that the printed parts are for the X Light Gantry from MamaBot.io, Created by Primesenator

https://www.instagram.com/primesenator/

https://www.etsy.com/listing/1611556116/voron-02-gantry?variation0=4127224961

These will NOT fit the X light Gantry from Fysect

Additionally, you will need to print the standard Tulip XY Bottoms.

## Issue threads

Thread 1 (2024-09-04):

Any chance for a NEMA 17 version?

Ataraxia-Mechanica, 2024-09-04:
https://www.printables.com/model/917398-voron-v02-nema-17
Basically this mod allows installing NEMA 17 motors at the expense of taking up 6 more millimeters of space in the back. Would be cool if it supports pins and double shear.

Driftrotor, 2024-09-17:
we have been looking at this to see how suitable it is, so far it looks promising but has the disadvantage of making the chamber hard to seal as it protrudes out of the back of the printer. also the standard bowden plate in between the AB motor mounts will not be able to be used.

Ataraxia-Mechanica, 2024-09-18:
I actually have designed a custom back plate to seal it, works pretty well but it is made in blender instead of cad.
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

Driftrotor, 2024-10-04:
we have added in a Beta Test for the Nema 17 AB Motor Mounts for testing. any feedback would be great

Ataraxia-Mechanica, 2024-10-04:
Uh oh
I only have 20mm shaft motors and it's kinda hard to find long shaft high current motors where I live

Driftrotor, 2024-10-04:
no worries, to be fair there are plenty of good nema 14's out on the market and lots of users report good performance from these.
these might be more readily available where you are too.

Closed 2024-10-04.

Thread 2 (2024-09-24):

Switch BOM to Google Drive Sheets Document

Nyshan, 2024-09-24:
Most projects that have BOMs are using Google Drive Sheets documents in order to allow for faster and easier alterations. Sources and availability can change rapidly being able to make that change without a PR can be extremely beneficial!

Amekyras, 2024-09-24:
I like this idea - will make the switch soon

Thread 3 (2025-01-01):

Belts Interfere With Tensioners

Nyshan, 2025-01-01:
When Y axis is at Y0 belt path can conflict with tensioners.
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

Driftrotor, 2025-02-07:
ok i will have a look into this.

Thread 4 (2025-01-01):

Belt Misalignment at Front Tensioners

Nyshan, 2025-01-01:
There appears to be some problems with belt alignment at the front tensioners. As far as I am able to discern, the XY joints and motor mounts are likely unaffected.
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

Any value in the Z-Axis using an integer or decimal that is not divisible by 0.2 (I'm assuming this number as it is the standard Voron layer height) will cause the user's slicer to cull certain features of an object. In this case small numbers like 0.05mm will likely be reduced to 0.

Strangely, in practice, I was able to add a total of 0.6mm to the surface the bearing stack rests on before alignment seemed to be correct. I'm not sure why this was the case for as the CAD doesn't feature any error of this magnitude.

Using stock STLs (mostly) the bottom flanges of my XY joint bearing appear to be higher than the bottom flanges of my tensioner bearings:

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

After adding 0.55mm (technically 0.6mm because of slicer stuff) to the surface the tensioner bearing stack rests on:

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

I understand that perspective make judging the above photos somewhat difficult but I hope they convey what I am trying to communicate.

Nyshan, 2025-01-01:
Please ignore any parts that appear to be missing (i.e. plastite) as I have been testing and re-fitting many different things in order to confirm theories and ideas I've had.

Driftrotor, 2025-03-20:
@Nyshan i believe that the issue has now been found (reference posts from the Discord) and that this issue has now been corrected.
if you are happy i think we can call this one solved and close this issue?

Closed 2025-03-22.

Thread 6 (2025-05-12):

All instances of reaming are misspelled

SnoWFLakE0s, 2025-05-12:
I'm just passing by--but I did notice that every time "reaming" is meant the word reeming is used, which is not a real word. Reaming is the proper terminology for the precise drilling of a hole.

Amekyras, 2025-05-12:
will fix <3

Driftrotor, 2025-06-11:
this should be fixed now and all docs updated with the correct spelling

Closed 2025-06-11.

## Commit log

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2024-07-06 CAD update
    removed all unnecessary materials
    simplified parts tree
    corrected Voron logo (mgn9)
2024-07-07 added XY joints to pim mod
    updated BOM
    updated CAD
    Updated PICS folder
    [BOM.csv]
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2024-07-07 STL update
    Updated superseded stl's
    added XY joints
    [Idler_Static_Bottom_A_x1.stl, Idler_Static_Bottom_B_x1.stl, Idler_Static_Top_A_x1.stl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]
2024-07-10 Big Update
    CAD updated
    STL's updated
    Tools added
    Renders updated
    [A_Idler_Static_x1.stl.stl, B_Idler_Static_x1.stl.stl, Bearing press tool.stl.stl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]
2024-07-11 STL's updated
    STL name corrections
    [A_Idler_Static_x1.stl, B_Idler_Static_x1.stl, Bearing press tool.stl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]
2024-07-11 Fixed slider STLs
    [Slider_Bottom_A_x1.stl, Slider_Bottom_B_x1.stl, Slider_Top_A_x1.stl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]
2024-08-06 Update BOM.csv
    changed FSCS to FHCS fixings for XY Joints
    [BOM.csv]
2024-08-08 Cad / STL update
    New CAD update
    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
    [A_Idler_Static_LazyCam_x1.stl, A_Idler_Static_x1.stl, B_Idler_Static_LazyCam_x1.stl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]
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2024-08-24 CAD / STL UPADTE
    names changed in CAD and in STL's
    readme updated
    [Idler_A_Tensioner_Lower_x1.stl, Idler_A_Tensioner_Upper_x1.stl, Idler_B_Tensioner_Lower_x1.stl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]
2024-09-04 CAD Update
    corrected AB MGN9 top mounts
    added tool for motor pullies
    [Pully Tool.stl, Top_Mount_A_MGN9C_x1.stl, Top_Mount_B_MGN9C_x1.stl]
2024-09-16 CAD update
    added MGN9H BETA
    added PIN GUIDE
    CAD upadte
    [A_Idler_Static_LazyCam_x1.stl, A_Idler_Static_x1.stl, BOM.csv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]
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2024-10-04 Big Update
    CAD house keeping
    added 18mm idler tensioners
    added nema 17 Beta
    added X Light Gantry Beta
    added ReadMe's
    added STL's
    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
    [A_Idler_Static_LazyCam_x1.stl, A_Idler_Static_x1.stl, BOM.csv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]
2024-11-04 STL update
    all stl's updated to latest CAD version
    added MMU XY joints
    added MMU umbilical plate
    added umbilical plate
    [A_Idler_Static_LazyCam_x1.stl, A_Idler_Static_x1.stl, B_Idler_Static_LazyCam_x1.stl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]
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2024-11-28 A New Era
    CAD added for 35mm shaft nema 14's
    CAD added for Live idlers (XY joints)
    STL's added for both
    [A_Idler_Static_LazyCam_x1.stl, A_Idler_Static_x1.stl, B_Idler_Static_LazyCam_x1.stl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]
2024-11-28 A NEW ERA
    updated Main CAD
    [Leftt_Idler_Tool.stl, Right_Idler_Tool.stl, XY Upper MMU.3mf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]
2024-11-28 A NEW ERA
    18mm pin idler tensioner now the standard
    [A_Idler_Static_LazyCam_x1.stl, A_Idler_Static_x1.stl, B_Idler_Static_LazyCam_x1.stl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]
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2024-11-28 A NEW ERA
    BOM updated
    [BOM.csv]
2024-12-01 A NEW ERA
    CAD update - pin cutting tool
    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
    [Pin_Jig_Bottom.stl, Pin_Jig_Top.stl]
2024-12-11 Update
    CAD update to V34
    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
    [MMU XY Joint Tops.stl, XY_Joint_Upper_Left_MMU.stl, XY_Joint_Upper_Right_MMU.stl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]
2024-12-11 update
    removed mgn7h stl file
    [Mount_Plate_A_x1.stl, Mount_Plate_B_x1.stl, Top_Mount_A_x1.stl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]
2025-02-04 QOL Update
    CAD Update v35
    QOL update - Tension Idlers
    QOL update - AB motor mounts
    [A_Idler_Static_LazyCam_x1.3mf, A_Idler_Static_LazyCam_x1.stl, A_Idler_Static_x1.3mf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]
2025-02-04 QOL Update
    V3 CAD - Live Idlers
    New spacer design
    QOL improvements - Lower XY Joints
    [XY_Joint_Left_Lower.3mf, XY_Joint_Left_Lower.stl, XY_Joint_Right_Lower.3mf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]
2025-02-11 QOL
    added missing upper XY joints to STL's folder
    [[a]_XY_Joint_Left_Upper_x1.stl, [a]_XY_Joint_Right_Upper_x1.stl]
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2025-02-12 organised print files
    .3mf print files have now been changed to .stl
    [A_Idler_Static_LazyCam_x1.3mf, A_Idler_Static_LazyCam_x1.stl, A_Idler_Static_x1.3mf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]
2025-06-06 small update
    top mount AB mgn9h / c had locating index resized to correct a fitment issue
    [Top_Mount_A_MGN9C_x1.stl, Top_Mount_A_MGN9H_x1.stl, Top_Mount_B_MGN9C_x1.stl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]
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2025-07-29 Tulip 2.0
    Updated CAD
    Updated STL's
    BOM changes
    some readme files updated
    [A_Idler_Static_LazyCam_x1.stl, A_Idler_Static_x1.stl, BOM.csv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]
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2025-08-02 Tulip 2.0
    updated spacer_hex for live idler
    this now uses the stock 9mm tall spacer as with the rest of Tulip
    [Sapcer_Hex_x6.stl, [a]_XY_Joint_spacer_hex_x4.stl, [a]_XY_Joint_spacer_hex_x6.stl]
2025-08-04 First UserMod
    UserMod for LDO door sitting proud
    [A_Idler_Static_(live_idler)+2mm_x1.stl, A_Idler_Static_+2mm_x1.stl, A_Idler_Static_LazyCam_(live_idler)+2mm_x1.stl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]
2025-08-21 Update BOM.csv
    updated BOM to give clearer BOM for Live Idlers XY Joints
    [BOM.csv]
2025-08-21 BOM Update
    BOM additions - live idler now has seperate BOM in the list
    [BOM.csv, BOM.xlsx]
2025-08-21 BOM update
    added Live idler to BOM
    [BOM.csv]
2025-08-23 Small update to 2mm usermod
    reorientated parts
    [A_Idler_Static_(live_idler)+2mm_x1.stl, A_Idler_Static_+2mm_x1.stl, A_Idler_Static_LazyCam_(live_idler)+2mm_x1.stl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]
2025-09-23 Update 2mm usermod
    Updated the 2mm height increase mod to fix an issue with the stock idler mounts which raised the screws 2mm
    [A_Idler_Static_+2mm_x1.stl, A_Idler_Static_LazyCam_+2mm_x1.stl, B_Idler_Static_+2mm_x1.stl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]
2025-10-20 Tulip 2.0
    STL's location change for live idler tension idlers - moved to tension idlers folder
    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
    [A_Idler_Static_LazyCam_x1.stl, A_Idler_Static_x1.stl, B_Idler_Static_LazyCam_x1.stl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]
2025-10-20 Tulip 2.0
    Updated the live idler stl's to show "Live" in the file name
    [A_Live_Idler_Static_LazyCam_x1.stl, A_Live_Idler_Static_x1.stl, B_Live_Idler_Static_LazyCam_x1.stl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]
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2025-10-21 Tulip 2.0
    Repo Update and organise
    new STL layout / Structure
    readme's updated
    [A_Idler_Static_LazyCam_x1.stl, A_Idler_Static_x1.stl, A_Live_Idler_Static_LazyCam_x1.stl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]
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2025-10-21 Tulip 2.0
    BOM updated with new links and page formatted correctly
    added PDF version with working links
    [BOM.csv, BOM.xlsx]
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2025-10-22 Tulip 2.0
    Added CAD for experimetal nema17 2WD and 4WD
    added STL's for both
    [Mount_Plate_A_x1.stl, Mount_Plate_B_x1.stl, Mount_Plate_x1.stl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]
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2025-10-23 Restructure documentation and CAD file organization
    Moved CAD, BOM, images, and guides into a new documentation folder structure for improved organization. Updated README.md to include BOM tables, clearer instructions, and local image references. Old 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
    [BOM.csv, BOM.xlsx]
2025-10-23 Fix typos and rename STL files for consistency
    Corrected spelling errors in STL filenames ('Sapcer' to 'Spacer') in both LIVE TULIP and OEM TULIP directories. Updated README.md to fix typos in 'available' and 'knowledge'.
    [Spacer_Hex_x6.stl]
2025-10-23 Rename STL files for improved folder structure
    STL files were moved to new directories with standardized naming conventions for better organization and clarity. Also fixed a typo in the old release notes documentation.
    [A_Idler_Static_LazyCam_x1.stl, A_Idler_Static_x1.stl, B_Idler_Static_LazyCam_x1.stl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]
